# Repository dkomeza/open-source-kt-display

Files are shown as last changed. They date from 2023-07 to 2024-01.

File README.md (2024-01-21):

[][contributors-url]
[][forks-url]
[][issues-url]
[][license-url]

# Open-Source KT Display
Open source display firmware for E-Bike KT controllers. Made for Arduino with compatible SPI Display. 

**NOTE**: _This repository is no longer supported or updated by @dkomeza. It has been moved to [oskd](https://github.com/dkomeza/oskd) where it will be maintained from now on (21.01.2024). If you wish to continue to develop this code yourself, I recommend you fork it._</code>

<br>

## TL;DR
This is an open source display created for KT controllers. It uses ESP32 and a compatible SPI display. It is a work in progress and is not yet ready for production.

<br>

## Table of contents

- [Open-Source KT Display](#open-source-kt-display)
  - [TL;DR](#tldr)
  - [Table of contents](#table-of-contents)
  - [About the project](#about-the-project)
    - [Features](#features)
    - [Future of the project](#future-of-the-project)

<br><br>

## About the project

This project started as a way to use a torque sensor with the KT controllers. Later I decided to create a full featured display for the KT controllers. The goal is to create a display that is open source and can be used with any KT controller. It will also have a torque sensor input and a legal speed and power limiter. It is still a work in progress and is not yet ready for production. For more information about the project, please visit the [wiki](https://github.com/dkomeza/open-source-kt-display/wiki).

<br>

### Features
 - Open source
 - Cheap to build yourself
 - Has a torque sensor input
 - Has a legal speed and power limiter
<br>

### Future of the project

As for now, the project is still in development. I am working on the firmware and the hardware. The firmware is finally usable but still not final and the hardware is not yet ready for production. On the software side I am currently working on the settings menu and bug fixes, and on the hardware I am working on the PCB design and the case design. I will release the firmware and the hardware design files when they are ready. I will also release a tutorial on how to build the display yourself.

<!-- MARKDOWN LINKS & IMAGES -->
<!-- https://www.markdownguide.org/basic-syntax/#reference-style-links -->
[contributors-shield]: https://img.shields.io/github/contributors/dkomeza/open-source-kt-display.svg?style=for-the-badge
[contributors-url]: https://github.com/dkomeza/open-source-kt-display/graphs/contributors
[forks-shield]: https://img.shields.io/github/forks/dkomeza/open-source-kt-display.svg?style=for-the-badge
[forks-url]: https://github.com/dkomeza/open-source-kt-display/network/members
[stars-shield]: https://img.shields.io/github/stars/dkomeza/open-source-kt-display.svg?style=for-the-badge
[stars-url]: https://github.com/dkomeza/open-source-kt-display/stargazers
[issues-shield]: https://img.shields.io/github/issues/dkomeza/open-source-kt-display.svg?style=for-the-badge
[issues-url]: https://github.com/dkomeza/open-source-kt-display/issues
[license-shield]: https://img.shields.io/github/license/dkomeza/open-source-kt-display.svg?style=for-the-badge
[license-url]: https://github.com/dkomeza/open-source-kt-display/blob/master/LICENSE.txt

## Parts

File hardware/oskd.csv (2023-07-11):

Source: | C:\Users\dawid\Desktop\Github\open-source-kt-display\pcb_design\pcb_design.kicad_sch
Date: | 22.05.2023 14:15:03
Tool: | Eeschema 7.0.2
Generator: | C:\Program Files\KiCad\7.0\bin\scripting\plugins/bom_csv_grouped_by_value.py
Component Count: | 33
Collated Components:
Item | Qty | Reference(s) | Value | LibPart | Footprint | Datasheet | DNP
1 | 1 | CFF1 | C | Device:C | Capacitor_SMD:C_1206_3216Metric_Pad1.33x1.80mm_HandSolder | ~
2 | 6 | CIN1, CIN2, CIN3, COUT1, COUT2, COUT3 | C | Device:C | Capacitor_SMD:C_1210_3225Metric_Pad1.33x2.70mm_HandSolder | ~
3 | 4 | CSMALL1, CSMALL2, CSMALL3, CSMALL4 | C | Device:C | Capacitor_SMD:C_1206_3216Metric | ~
4 | 1 | D1 | S310 | Diode:1.5KExxA | KT_Display:S2M | https://www.vishay.com/docs/88301/15ke.pdf
5 | 1 | J1 | BUTTON_CONNECTOR | Connector_Generic:Conn_01x04 | KT_Display:SolderWire-1x4-buttons | ~
6 | 1 | J2 | Conn_Programming | Connector_Generic:Conn_01x06 | Connector_PinHeader_2.54mm:PinHeader_1x06_P2.54mm_Horizontal | ~
7 | 1 | J3 | Conn_Brake | Connector_Generic:Conn_01x02 | Connector_Wire:SolderWire-0.25sqmm_1x02_P4.5mm_D0.65mm_OD2mm | ~
8 | 1 | J4 | THERMISTOR_CONNECTOR | Connector_Generic:Conn_01x02 | Connector_Wire:SolderWire-0.25sqmm_1x02_P4.2mm_D0.65mm_OD1.7mm | ~
9 | 1 | L1 | L | Device:L | Inductor_SMD:L_7.3x7.3_H3.5 | ~
10 | 2 | Q1, Q2 | BSS123 | Transistor_FET:BSS123 | Package_TO_SOT_SMD:SOT-23 | http://www.diodes.com/assets/Datasheets/ds30366.pdf
11 | 1 | R1 | 30K | Device:R | Resistor_SMD:R_1206_3216Metric_Pad1.30x1.75mm_HandSolder | ~
12 | 2 | R2, R4 | 10K | Device:R | Resistor_SMD:R_1206_3216Metric_Pad1.30x1.75mm_HandSolder | ~
13 | 1 | R3 | 5R0 | Device:R | Resistor_SMD:R_1206_3216Metric_Pad1.30x1.75mm_HandSolder | ~
14 | 1 | RB1 | 56k | Device:R | Resistor_SMD:R_1206_3216Metric_Pad1.30x1.75mm_HandSolder | ~
15 | 1 | RB2 | 1M | Device:R | Resistor_SMD:R_1206_3216Metric_Pad1.30x1.75mm_HandSolder | ~
16 | 1 | RRX1 | 3.3k | Device:R | Resistor_SMD:R_1206_3216Metric_Pad1.30x1.75mm_HandSolder | ~
17 | 1 | U1 | Connection_Display | KT_Display:Connection_Display | KT_Display:SolderWire-1x5-display
18 | 1 | U2 | ESP32-WROOM-32D | RF_Module:ESP32-WROOM-32D | RF_Module:ESP32-WROOM-32 | https://www.espressif.com/sites/default/files/documentation/esp32-wroom-32d_esp32-wroom-32u_datasheet_en.pdf
19 | 1 | U3 | XL7015E1 | KT_Display:XL7015E1 | Package_TO_SOT_SMD:TO-252-5_TabPin3
20 | 1 | U4 | NCP1117-3.3_SOT223 | Regulator_Linear:NCP1117-3.3_SOT223 | Package_TO_SOT_SMD:SOT-223-3_TabPin2 | http://www.onsemi.com/pub_link/Collateral/NCP1117-D.PDF
21 | 1 | U5 | BTS4140N | KT_Display:BTS4140N | Package_TO_SOT_SMD:SOT-223-3_TabPin2
22 | 1 | U6 | LM1117-1.8 | Regulator_Linear:LM1117-1.8 | Package_TO_SOT_SMD:SOT-223-3_TabPin2 | http://www.ti.com/lit/ds/symlink/lm1117.pdf
23 | 1 | U7 | ST7789VS | OSKD:ST7789VS | OSKD:ST7789V2

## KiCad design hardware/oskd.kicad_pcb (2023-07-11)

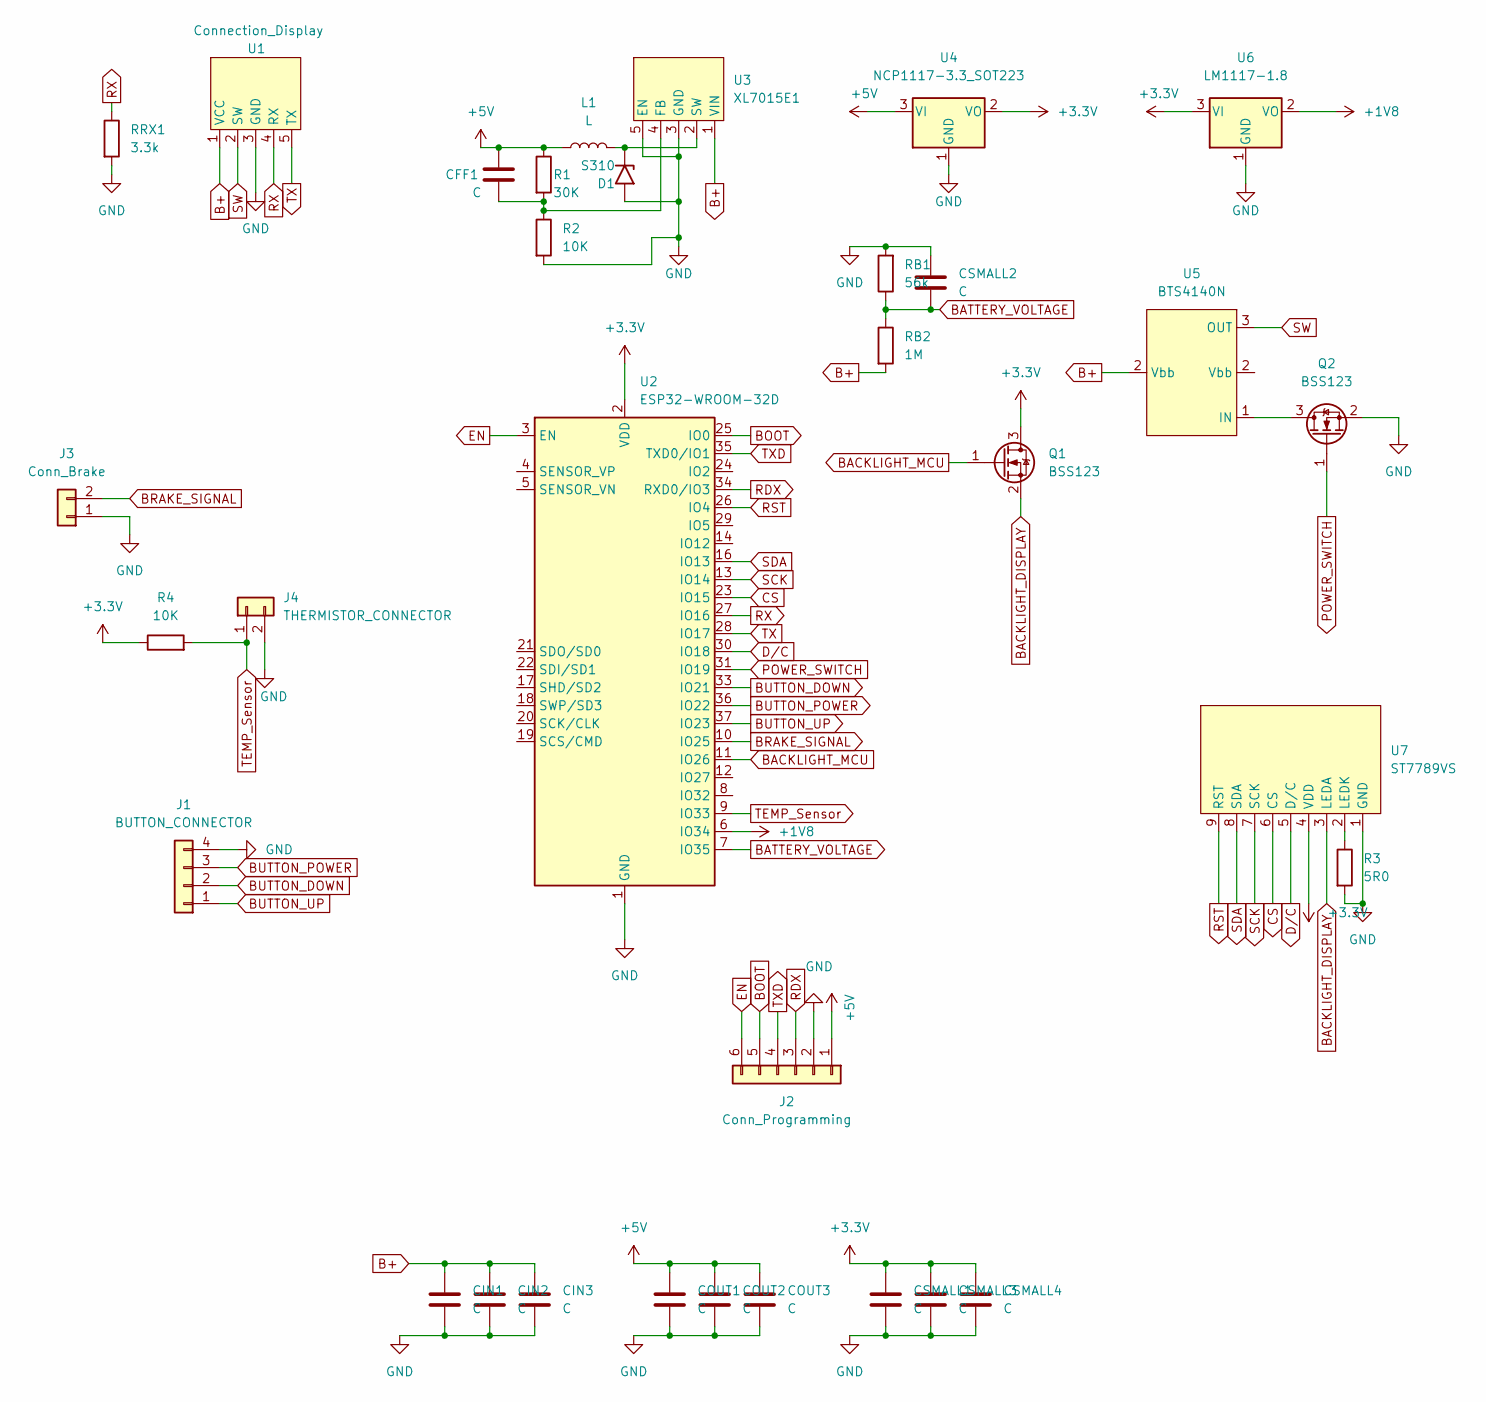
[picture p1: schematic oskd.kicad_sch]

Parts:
CFF1: C; C_1206_3216Metric_Pad1.33x1.80mm_HandSolder
CIN1, CIN2, CIN3: C; C_1210_3225Metric_Pad1.33x2.70mm_HandSolder
COUT1, COUT2, COUT3: C; C_1210_3225Metric_Pad1.33x2.70mm_HandSolder
CSMALL1, CSMALL2, CSMALL3, CSMALL4: C; C_1206_3216Metric
D1: S310; S2M
J1: BUTTON_CONNECTOR; SolderWire-1x4-buttons
J2: Conn_Programming; PinHeader_1x06_P2.54mm_Horizontal
J3: Conn_Brake; SolderWire-0.25sqmm_1x02_P4.5mm_D0.65mm_OD2mm
J4: THERMISTOR_CONNECTOR; SolderWire-0.25sqmm_1x02_P4.2mm_D0.65mm_OD1.7mm
L1: L; L_7.3x7.3_H3.5
Q1, Q2: BSS123; SOT-23
R1: 30K; R_1206_3216Metric_Pad1.30x1.75mm_HandSolder
R2, R4: 10K; R_1206_3216Metric_Pad1.30x1.75mm_HandSolder
R3: 5R0; R_1206_3216Metric_Pad1.30x1.75mm_HandSolder
RB1: 56k; R_1206_3216Metric_Pad1.30x1.75mm_HandSolder
RB2: 1M; R_1206_3216Metric_Pad1.30x1.75mm_HandSolder
RRX1: 3.3k; R_1206_3216Metric_Pad1.30x1.75mm_HandSolder
U1: Connection_Display; SolderWire-1x5-display
U2: ESP32-WROOM-32D; ESP32-WROOM-32
U3: XL7015E1; TO-252-5_TabPin3
U4: NCP1117-3.3_SOT223; SOT-223-3_TabPin2
U5: BTS4140N; SOT-223-3_TabPin2
U6: LM1117-1.8; SOT-223-3_TabPin2
U7: ST7789VS; ST7789V2

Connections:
+1V8: U2.6 (IO34), U6.2 (VO)
+3.3V: CSMALL1.1, CSMALL3.1, CSMALL4.1, Q1.3 (D), R4.1, U2.2 (VDD), U4.2 (VO), U6.3 (VI), U7.4 (VDD)
+5V: CFF1.2, COUT1.1, COUT2.1, COUT3.1, J2.1, L1.1, R1.1, U4.3 (VI)
B+: CIN1.1, CIN2.1, CIN3.1, RB2.2, U1.1 (VCC), U3.1 (VIN), U5.2 (Vbb)
BACKLIGHT_DISPLAY: Q1.2 (S), U7.3 (LEDA)
BACKLIGHT_MCU: Q1.1 (G), U2.11 (IO26)
BATTERY_VOLTAGE: CSMALL2.2, RB1.1, RB2.1, U2.7 (IO35)
BOOT: J2.5, U2.25 (IO0)
BRAKE_SIGNAL: J3.2, U2.10 (IO25)
BUTTON_DOWN: J1.2, U2.33 (IO21)
BUTTON_POWER: J1.3, U2.36 (IO22)
BUTTON_UP: J1.1, U2.37 (IO23)
CS: U2.23 (IO15), U7.6 (CS)
D/C: U2.30 (IO18), U7.5 (D/C)
EN: J2.6, U2.3 (EN)
GND: CIN1.2, CIN2.2, CIN3.2, COUT1.2, COUT2.2, COUT3.2, CSMALL1.2, CSMALL2.1, CSMALL3.2, CSMALL4.2, D1.2 (A2), J1.4, J2.2, J3.1, J4.2, Q2.2 (S), R2.2, R3.2, RB1.2, RRX1.2, U1.3 (GND), U2.1 (GND), U2.15 (GND), U2.38 (GND), U2.39 (GND), U3.3 (GND), U3.5 (EN), U4.1 (GND), U6.1 (GND), U7.1 (GND)
unnamed: CFF1.1, R1.2, R2.1, U3.4 (FB)
unnamed: D1.1 (A1), L1.2, U3.2 (SW)
unnamed: Q2.3 (D), U5.1 (IN)
unnamed: R3.1, U7.2 (LEDK)
POWER_SWITCH: Q2.1 (G), U2.31 (IO19)
RDX: J2.3, U2.34 (RXD0/IO3)
RST: U2.26 (IO4), U7.9 (RST)
RX: RRX1.1, U1.4 (RX), U2.27 (IO16)
SCK: U2.13 (IO14), U7.7 (SCK)
SDA: U2.16 (IO13), U7.8 (SDA)
SW: U1.2 (SW), U5.3 (OUT)
TEMP_Sensor: J4.1, R4.2, U2.9 (IO33)
TX: U1.5 (TX), U2.28 (IO17)
TXD: J2.4, U2.35 (TXD0/IO1)

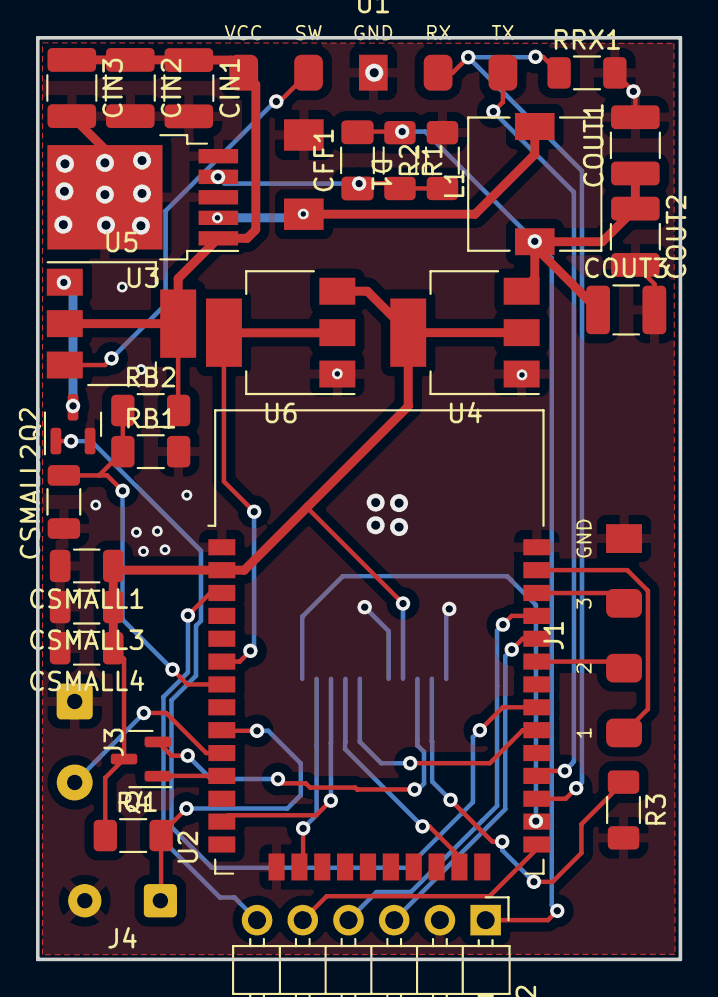
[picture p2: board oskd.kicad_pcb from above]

Board: 2 copper layers, 35.7 x 51.2 mm, 33 parts (1 on the bottom side), 30 nets.

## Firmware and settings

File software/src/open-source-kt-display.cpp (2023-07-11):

#include <Arduino.h>

#include "connection/OTA.h"
#include "controller/controller.h"
#include "data/data.h"
#include "io/io.h"
#include "screen/screen.h"
#include "settings/settings.h"

Controller controller;
Data data;
IO io;
Screen screen;
Settings settings;

long lastUpdate = 0;

bool rising = true;

const int POWER_PIN = 19;
const int POWER_BUTTON_PIN = 27;

void handleWakeUp();

void setup()
{
    gpio_hold_dis(GPIO_NUM_19);
    gpio_hold_dis(GPIO_NUM_26);

    pinMode(POWER_PIN, OUTPUT);
    pinMode(POWER_BUTTON_PIN, INPUT_PULLUP);
    esp_sleep_enable_ext0_wakeup((gpio_num_t)POWER_BUTTON_PIN, 0);

    handleWakeUp();

    controller.setup();
    screen.setup();
    io.setup();
    settings.setup();

    screen.setBrightness(1);

    setupOTA();

    delay(400);
    lastUpdate = millis();
}

void loop()
{
    controller.update();
    screen.update();
    io.update();

    ArduinoOTA.handle();

    if (millis() - lastUpdate < 50)
    {
        delay(50 - (millis() - lastUpdate));
    }

    lastUpdate = millis();
}

void handleWakeUp()
{
    if (digitalRead(POWER_BUTTON_PIN) != LOW)
    {
        esp_deep_sleep_start();
    }
    delay(1000);
    if (digitalRead(POWER_BUTTON_PIN) != LOW)
    {
        esp_deep_sleep_start();
    }
    digitalWrite(POWER_PIN, HIGH);
}

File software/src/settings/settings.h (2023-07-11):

#ifndef OSKD_SETTINGS_H
#define OSKD_SETTINGS_H

#include <Arduino.h>
#include <EEPROM.h>

#include "../data/data.h"
#include "../screen/screen.h"

class Settings
{
private:
    static const int MENU_SIZE = 15;
    static const int BUFFER_SIZE = 13;
    static const int EEPROM_SIZE = 512;

    static const int GEAR_EEPROM_ADDRESS = 20;
    static const int LEGAL_MODE_EEPROM_ADDRESS = 21;

    static const int MAX_GEAR = 5;
    static const int MIN_GEAR = 0;
    static const int MAX_SPEED_LIMIT = 72;
    static const int MIN_SPEED_LIMIT = 10;

    const String names[MENU_SIZE] = {"Speed limit", "Wheel size", "P1", "P2", "P3", "P4", "P5", "C1", "C2", "C4", "C5", "C11", "C12", "C13", "C14"};
    int values[MENU_SIZE];
    const int minValues[MENU_SIZE] = {10, 0, 0, 0, 0, 0, 0, 0, 0, 0, 0, 0, 0, 0, 1};
    const int maxValues[MENU_SIZE] = {72, 14, 255, 6, 1, 1, 30, 7, 7, 4, 10, 3, 7, 5, 3};
    const int defaultValues[MENU_SIZE] = {72, 12, 86, 1, 1, 0, 13, 5, 0, 0, 10, 0, 4, 0, 1};
    const int wheelSizeTable[15][2] = {{50, 22}, {60, 18}, {80, 10}, {100, 14}, {120, 2}, {140, 6}, {160, 0}, {180, 4}, {200, 8}, {230, 12}, {240, 16}, {260, 20}, {275, 24}, {280, 28}, {290, 30}}; // {wheel size * 10, byte value}

    int *SPEED_LIMIT = &values[0];
    int *WHEEL_SIZE = &values[1];
    int *P1 = &values[2];
    int *P2 = &values[3];
    int *P3 = &values[4];
    int *P4 = &values[5];
    int *P5 = &values[6];
    int *C1 = &values[7];
    int *C2 = &values[8];
    int *C4 = &values[9];
    int *C5 = &values[10];
    int *C11 = &values[11];
    int *C12 = &values[12];
    int *C13 = &values[13];
    int *C14 = &values[14];

    int currentGear = 0;
    int previousGear = 0;

    bool legalMode = false;

    int speedLimit = *SPEED_LIMIT;

    bool checkInitialSettings();
    void loadSettings();

    void calculatePacket();
    byte calculateChecksum(byte buffer[]);

    void loadGearFromEEPROM();
    void saveGearToEEPROM();
    void loadLegalModeFromEEPROM();
    void saveLegalModeToEEPROM();

public:
    void setup();

    byte settingsBuffer[BUFFER_SIZE];
    int menuSize = MENU_SIZE;
    String getOptionName(int index) const { return names[index]; }
    int getOptionValue(int index) const { return values[index]; }
    int getWheelSize(int value) const { return wheelSizeTable[value][0]; }

    int selectedOption = false;
    int cursorPosition = 0;

    void increaseOption();
    void decreaseOption();
    void selectOption();

    void setGear(int gear);
    void toggleLegalMode();
    void startWalkMode();
    void stopWalkMode();

    void saveSettings();
};

extern Settings settings;

#endif // OSKD_SETTINGS_H

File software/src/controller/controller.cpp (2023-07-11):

#include "./controller.h"

void Controller::setup()
{
    controllerSerial.begin(controllerBaudRate, SERIAL_8N1, controllerRXPin, controllerTXPin);
}

void Controller::update()
{
    sendData();
    receiveData();
}

void Controller::sendData()
{
    controllerSerial.write(data.settingsBuffer, BUFFER_UP_SIZE);
}

void Controller::receiveData()
{
    byte buffer[BUFFER_SIZE];

    byte firstByte = controllerSerial.peek();
    int counter = 0;

    while (firstByte != 65 && counter < 20)
    {
        controllerSerial.read();
        firstByte = controllerSerial.peek();
        counter++;
    }

    if (counter >= 20)
    {
        return;
    }

    if (controllerSerial.available() >= BUFFER_SIZE)
    {
        controllerSerial.readBytes(buffer, BUFFER_SIZE);
    }
    parseData(buffer);
}

void Controller::parseData(byte buffer[])
{
    bool isValid = isDataValid(buffer, 0);

    if (!isValid)
    {
        return;
    }

    if (buffer[3] + buffer[4] <= 0)
    {
        data.speed = 0;
    }
    else
    {
        data.speed = round(60000 / (buffer[3] << 8 | buffer[4]) * RPM_CONSTANT * 0.66);
    }

    if (data.speed < 2)
    {
        data.speed = 0;
    }

    data.batteryBars = buffer[1];

    if (data.batteryBars > 16)
    {
        data.batteryBars = 16;
    }

    data.power = buffer[8] * 13;
    data.temperature = int8_t(buffer[9]) + 15;

    bool brake = (buffer[7] & 32) == 32;

    if (brake)
    {
        data.gearState |= BRAKE;
    }
    else
    {
        data.gearState &= ~BRAKE;
    }
}

bool Controller::isDataValid(byte buffer[], int counter)
{
    int checksum = calculateChecksum(buffer);

    if (buffer[0] == 65 && buffer[6] == checksum)
    {
        return true;
    }

    if (counter >= 3)
    {
        return false;
    }

    byte newBuffer[BUFFER_SIZE];
    int shift = 0;

    for (int i = 1; i < BUFFER_SIZE; i++)
    {
        if (buffer[i] == 65)
        {
            shift = i;
        }
    }

    shift = BUFFER_SIZE - shift;

    for (int i = 0; i < BUFFER_SIZE; i++)
    {
        if (i < shift)
        {
            newBuffer[i] = buffer[BUFFER_SIZE + i - shift];
        }
        else
        {
            newBuffer[i] = buffer[i - shift];
        }
    }

    memcpy(buffer, newBuffer, sizeof(newBuffer));

    return isDataValid(buffer, counter + 1);
}

int Controller::calculateChecksum(byte buffer[])
{
    int crc = 0;
    for (int i = 0; i < BUFFER_SIZE; i++)
    {
        if (i != 6 && i != 0)
        {
            crc ^= buffer[i];
        }
    }
    return crc;
}

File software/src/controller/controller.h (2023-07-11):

#ifndef OSKD_CONTROLLER_H
#define OSKD_CONTROLLER_H

#include <Arduino.h>
#include <HardwareSerial.h>

#include "../data/data.h"
#include "../screen/screen.h"

class Controller
{
public:
    void setup();

    void update();

private:
    HardwareSerial controllerSerial = HardwareSerial(2);

    const int controllerBaudRate = 9600;
    const int controllerRXPin = 16;
    const int controllerTXPin = 17;

    const int BUFFER_UP_SIZE = 13;
    const int BUFFER_SIZE = 12;

    const double RPM_CONSTANT = 0.1885;

    void sendData();
    void receiveData();

    void parseData(byte buffer[]);
    bool isDataValid(byte buffer[], int counter);

    int calculateChecksum(byte buffer[]);
};

extern Controller controller;

#endif // OSKD_CONTROLLER_H

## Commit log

2022-09-13 Arduino button prototype
2022-09-13 Initial thermistor code
2022-09-13 Upload thermistor circuit
2022-09-13 Button circuit diagram upload
2022-09-13 Added README to Arduino tests
2022-09-13 [ImgBot] Optimize images
    *Total -- 21.88kb -> 8.84kb (59.63%)
    /testing/Arduino/button/button_circuit.png -- 9.76kb -> 3.85kb (60.53%)
    /testing/Arduino/thermistor/thermistor_circuit.png -- 12.13kb -> 4.99kb (58.9%)
2022-10-02 Protocol wheel size testing
2022-10-05 Wheel size option update
2022-10-11 Adapted code to use ESP32 instead of Arduino Nano
2022-10-18 [ImgBot] Optimize images
    /testing/Arduino/serial_read_v1.0/serial_circuit.png -- 22.34kb -> 6.39kb (71.39%)
2022-10-30 Engine temperature display fix
2022-11-09 Bump loader-utils in /prototype/web-parameters-calculator
    Bumps [loader-utils](https://github.com/webpack/loader-utils) from 2.0.2 to 2.0.3.
    - [Release notes](https://github.com/webpack/loader-utils/releases)
    - [Changelog](https://github.com/webpack/loader-utils/blob/v2.0.3/CHANGELOG.md)
    - [Commits](https://github.com/webpack/loader-utils/compare/v2.0.2...v2.0.3)
    ---
    updated-dependencies:
    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
2022-11-16 Bump loader-utils in /prototype/web-parameters-calculator
    Bumps [loader-utils](https://github.com/webpack/loader-utils) from 2.0.3 to 2.0.4.
    - [Changelog](https://github.com/webpack/loader-utils/blob/v2.0.4/CHANGELOG.md)
    - [Commits](https://github.com/webpack/loader-utils/compare/v2.0.3...v2.0.4)
    - dependency-name: loader-utils
    dependency-type: indirect
    ...
    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
2022-12-07 Fixed settings when powering on the first time
2022-12-08 Read, calculate and output torque
2022-12-10 Torque sensor basic implementation
2022-12-10 Added menu option for setting torque sensor delay (T1)
2022-12-10 Fixed torque sensor output
2022-12-14 Initial torque sensor gear support
2022-12-15 Added battery voltage reading
2022-12-15 Battery offset fix
2022-12-15 Changed battery voltage display location
2022-12-16 Battery voltage fix
2023-01-25 Torque sensor file bug fixes
2023-01-26 Added JSdoc to the torqueSensor file.
2023-01-26 Added pcb design
    [pcb_design.kicad_pcb, pcb_design.kicad_sch]
2023-02-03 Battery level display fix
2023-02-03 Changed P4 and C4 settings for the torque sensor
2023-02-10 Created custom button implementation
2023-04-06 Switch to PlatformIO
    [pcb_design.kicad_pcb, pcb_design.kicad_sch]
2023-04-06 Move .git directory
    [pcb_design.kicad_pcb, pcb_design.kicad_sch]
2023-04-06 Boot after holding the power button for one second
2023-04-07 Move the display init to prevent flash of white on restart
    [open-source-kt-display.cpp]
2023-06-09 :art: Change file structure
    [oskd.csv, oskd.kicad_pcb, oskd.kicad_sch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]
2023-06-09 :zap: Switch from .h files to .hpp
2023-07-08 :bug: Fix display not initializing
    [open-source-kt-display.cpp]
2023-07-08 :hammer: Refactor `settings` class
    Not complete - missing settings menu
    [open-source-kt-display.cpp, settings.h]
2023-07-11 :sparkles: Power switch & bug fixes
    [controller.cpp, controller.h, io.cpp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]

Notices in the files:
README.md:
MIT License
